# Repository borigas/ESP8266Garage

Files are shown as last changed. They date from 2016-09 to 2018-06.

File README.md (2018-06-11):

# ESP8266 Garage

Sensor and remote for garage door. Mounts on ceiling of garage and detects if the garage is open or closed and sends the status to an Mqtt relay. Also accepts messages from the relay to open and control the door.

### Photos:
https://goo.gl/photos/TKTH1ud8kynhA8XG7

### Circuit Diagram:
https://circuits.io/circuits/2474900-mqtt-garage-door-sensor

### Case Designs
https://tinkercad.com/things/8l6zTLbaJ09

### Part

| Part | Price |
|---|---|
| [Breadboard](http://www.electrodragon.com/product/small-size-breadboard-layout-pcb/) | $1.60 |
| [ESP8266](http://www.electrodragon.com/product/nodemcu-lua-amica-r2-esp8266-wifi-board/) | $4.70 |
| [US-100 3v Distance Sensor](https://www.amazon.com/gp/product/B00LQEUFHC/ref=oh_aui_detailpage_o04_s00?ie=UTF8&psc=1) | $2.20 |
| [JRC-21F 3v Relay](https://www.amazon.com/gp/product/B00LQEUFHC/ref=oh_aui_detailpage_o04_s00?ie=UTF8&psc=1) | $2.50 |
| 330Ω resistor | |
| 2n2222 transistor | |
| PLA for case | $4 |
| Total | $15 |

### Notes
- The amp is because the ESP8266 IO pins don't source enough current to trigger the relay. The 3v pin does though, so I use the current from that

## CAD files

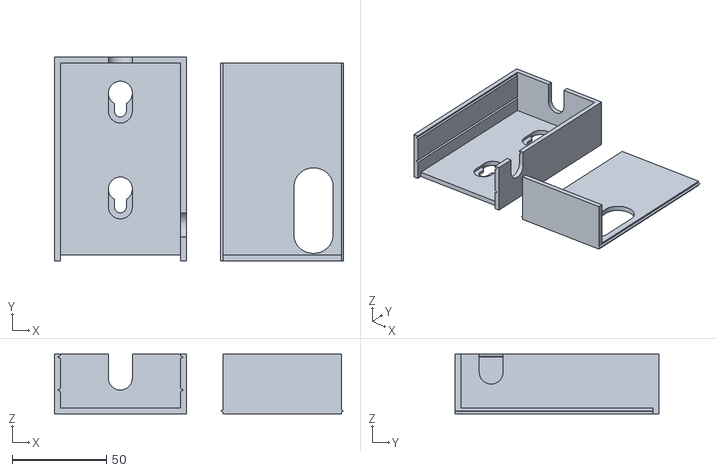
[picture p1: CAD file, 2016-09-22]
Case.stl
153.2 x 108.0 x 31.8

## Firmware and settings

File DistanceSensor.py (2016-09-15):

import machine

class DistanceSensor:

    def __init__(self, trigger, echo):
        self.lastHighTime = 0
    
        self.triggerPin = machine.Pin(0, machine.Pin.OUT)
        self.triggerPin.value(0)
        self.echoPin = machine.Pin(4, machine.Pin.IN)
        self.recentDistances = list()
        
    def Measure(self):
        self.triggerPin.value(1)
        #time.sleep(0.001)
        self.triggerPin.value(0)
        
        time = machine.time_pulse_us(self.echoPin, 1, 100000)
        dist = 165.7 * time * 3.28084 / 1000000
        #print("Dist: ", dist, " ft. Temp Timer: ", time)
        
        return dist
            
    def SmoothedMeasure(self):
        distanceTolerance = 0.2
        checkCount = 5
        distances = list()
        
        for i in range(checkCount):
            distance = self.Measure()
            if self.IsValidReading(distance):
                distances.append(distance)
        
        currentMeasurement = 0
        if len(distances) != 0:
            currentMeasurement = max(distances)
            self.recentDistances.append(currentMeasurement)
            if len(self.recentDistances) > checkCount:
                self.recentDistances.pop(0)
        
            firstNum = self.recentDistances[0]
            for num in self.recentDistances:
                if abs(firstNum - num) > distanceTolerance:
                    return 0
            
        return currentMeasurement
        
    def IsValidReading(self, distance):
        return 0.1 < distance < 25
            
    def IsDoorOpen(self, distance):
        return distance <= 4

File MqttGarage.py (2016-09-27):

import machine
import time
import ubinascii
import ujson

from Relay import Relay
from DistanceSensor import DistanceSensor
from MqttHelper import MqttHelper
    
class MqttGarage:
    
    def __init__(self):
        trigger = 0
        echo = 4
        relayPin = 5
        serverAddress = "192.168.1.12"
        
        self.distanceSensor = DistanceSensor(trigger, echo)
        
        self.relay = Relay(relayPin)
        
        self.clientId = str(ubinascii.hexlify(machine.unique_id()), "utf-8")
        self.mqttClient = MqttHelper(serverAddress, self.clientId)
        
        self.baseTopic = "home/garage/door/" + self.clientId
        self.setTopic = self.baseTopic + "/set"
        
        self.mqttClient.Subscribe(self.setTopic, self.SubscribeCallback)
        
        self.timer = machine.Timer(0)
        
        self.distance = 0
        self.isOpen = False
        self.hasRun = False
        self.hasNewMessage = False
        self.lastPublish = 0
        self.lastSubscribe = 0
        self.recentDistances = list()
        
    def timerCallback(self, timer):
        isTimeLocked = False
        if self.lastSubscribe != 0:
            now = time.time()
            lastSubscribeAge = now - self.lastSubscribe
            # Lock for 15s after receiving a message
            isTimeLocked = lastSubscribeAge < 15
        
        hadMessage = self.CheckMqttMessages(not isTimeLocked)
        if not isTimeLocked and not hadMessage:
            self.CheckDistance()
        
    def CheckMqttMessages(self, processMessages):
        self.mqttClient.CheckForMessage()
        hadMessage = self.hasNewMessage
        if hadMessage:
            self.hasNewMessage = False
            self.lastSubscribe = time.time()
            
            if processMessages:
                openMsg = b'open'
                closeMsg = b'close'
                currentMessage = self.lastMessage
                if currentMessage == openMsg:
                    self.ToggleDoor(True)
                elif currentMessage == closeMsg:
                    self.ToggleDoor(False)
            
        return hadMessage
    
        
    def SubscribeCallback(self, topic, msg):
        print("MsgReceived. Topic: ", topic, " Msg: ", msg)
        self.lastTopic = topic
        self.lastMessage = msg
        self.hasNewMessage = True
        
    def CheckDistance(self):
        distance = self.distanceSensor.SmoothedMeasure()
        
        now = time.time()
        lastPublishAge = now - self.lastPublish
        
        isOpen = self.distanceSensor.IsDoorOpen(distance)
        
        isValidReading = self.distanceSensor.IsValidReading(distance)
        
        hasDoorOpenChanged = isOpen != self.isOpen
        hasDistanceChanged = abs(distance - self.distance) > 0.2
        hasPublishExpired = lastPublishAge < 0 or lastPublishAge > 60 * 15 / 1.122833 # Clock isn't very accurate. Scale it back to real time
        
        #print("Dist:", distance, " HasRun:", self.hasRun, " IsValid:", isValidReading, " IsOpen:", isOpen, " CarPresent:", isCarPresent, " DoorChanged:", hasDoorOpenChanged, " CarChanged:", hasCarStatusChanged, " DistChanged:", hasDistanceChanged, " PubChanged:", hasPublishExpired, " PubAge:", lastPublishAge, " Now:", now, " Last:", self.lastPublish)
        
        if isValidReading and ((not self.hasRun) or hasDoorOpenChanged or hasDistanceChanged or hasPublishExpired):
        
            self.distance = distance
            self.isOpen = isOpen
            
            self.PublishStatus()
            
            self.lastPublish = now
            self.hasRun = True
            
    def PublishStatus(self):
        status = "closed"
        if self.isOpen:
            status = "open"
        
        dictionary = dict(
            Status = status,
            Distance = self.distance, 
            IsOpen = self.isOpen,
            ClientId = self.clientId,
        )
        msg = ujson.dumps(dictionary)
        topic = self.baseTopic
        print(topic + ": " + msg)
        self.mqttClient.Publish(topic, msg)
            
    def ToggleDoor(self, desiredIsOpen):
        distance = self.distanceSensor.SmoothedMeasure()
        
        expectedCurrentIsDoorUp = not desiredIsOpen
        
        if self.distanceSensor.IsValidReading(distance) and self.distanceSensor.IsDoorOpen(distance) == expectedCurrentIsDoorUp:
            self.relay.Close()
            time.sleep(0.1)
            self.relay.Open()
            
            self.isOpen = desiredIsOpen
            
            self.PublishStatus()
        
    def StartTimer(self):
        self.timer.init(period=1000, mode=machine.Timer.PERIODIC, callback=self.timerCallback)
        
    def StopTimer(self):
        self.timer.deinit()

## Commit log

2016-07-19 Basic trigger and led toggle test
2016-07-20 Playing with distance sensor. Looks like it needs 5v
2016-07-31 Added distance sensor
2016-09-13 More smoothing of sensor results
2016-09-15 Update simple to most recent simple.py to get around connection problems
    [simple.py]
2016-09-15 Split files out to try to make compile footprint smaller
2016-09-15 Removed some methods to reduce memory footprint
2016-09-22 Added case link and cost
2016-09-22 Added case design
    [Case.stl]
